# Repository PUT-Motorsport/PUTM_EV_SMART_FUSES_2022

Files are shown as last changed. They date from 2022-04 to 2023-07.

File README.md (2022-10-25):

# PUTM_EV_SMART_FUSES_2022

## Description
The main principle behind the concept of Smart Fuses was adaptability and ease of resetting fuses, what the past designs couldn't achive. The board uses VN9D30Q100F High-side driver with integrated short-circuit detection and programmable interface based on reliable and fast SPI communication. It features 6 programmable channels, two of them are rated for 31,5A maximum flowing current the rest is rated for 14A. As mentioned used uCs can detect when one of the managed boards are

## Quick preview
The Smart Fuses board is responsible for two primary things:
- control over chips with integrated fuses based on mosfets,
- control over assi (auyonomus system status indicator) and buzzer.

## Basic flow chart
Flow chart drawio (1) <br/>
( basic concept of the program's flow, it may or may not change depending on the needs )

## Main Connector Pinout


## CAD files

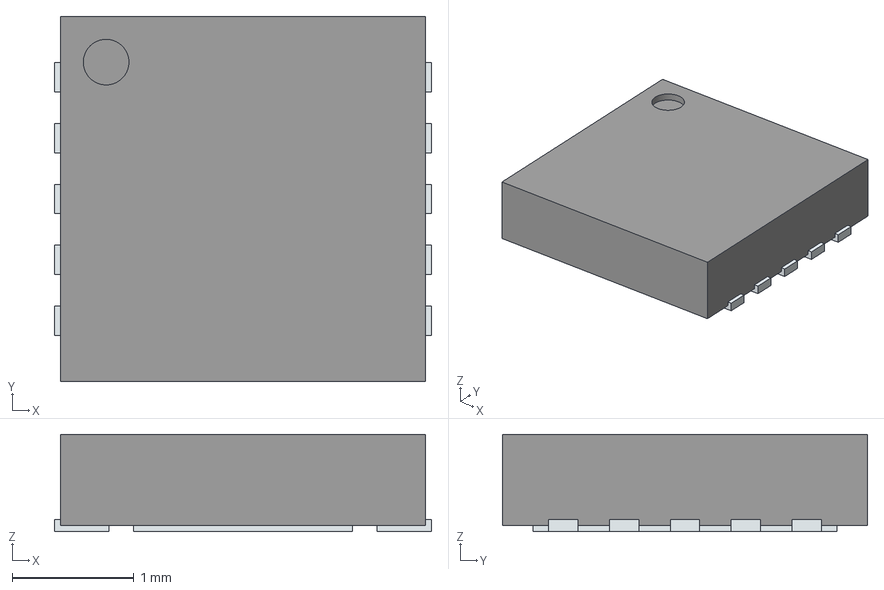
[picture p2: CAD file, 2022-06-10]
hardware/NIS4461MT1TXG/NIS4461MT1TXG.stp
3.10 x 3.00 x 0.8 mm
ThermalPin
PinsArrayLR

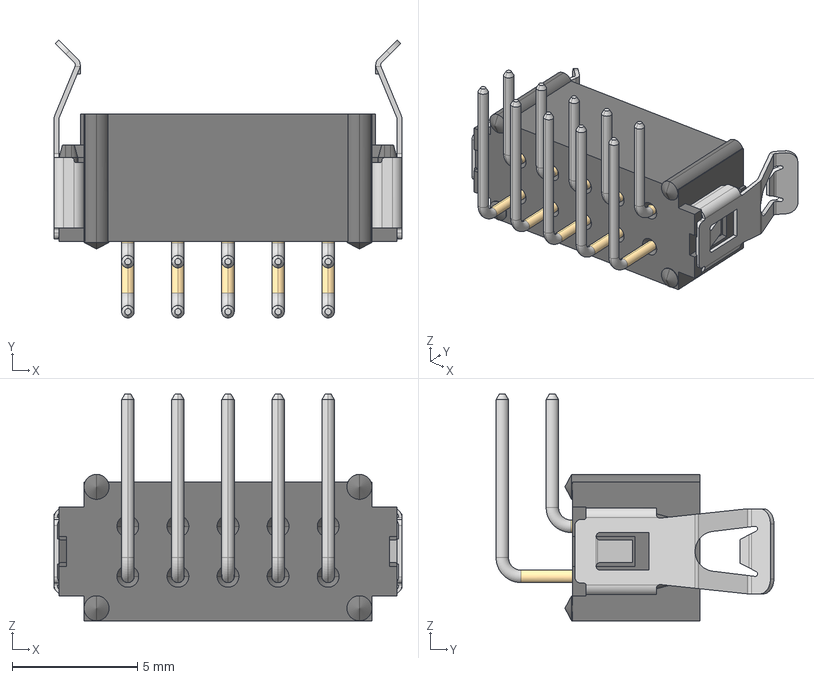
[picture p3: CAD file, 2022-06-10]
hardware/M80-8661022/M80-8661022.stp
13.9 x 11.1 x 9.05 mm
M80-1021098_SEPARATE_ROWS
M80-868-PIN1 x 5
M80-868-PIN2 x 5
M80-001XXXX x 2

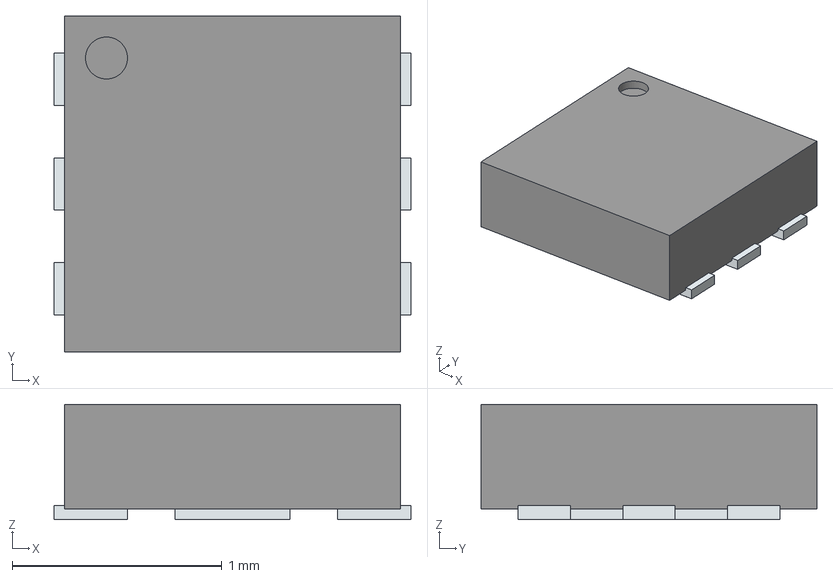
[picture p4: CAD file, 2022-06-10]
hardware/NCS20061MUTAG/NCS20061MUTAG.stp
1.70 x 1.60 x 0.55 mm
ThermalPin
PinsArrayLR

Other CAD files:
hardware/NIS6351MT2TXG/NIS6351MT2TXG.stp
hardware/NCS20061MUTAG/NCS20061MUTAG.stl
hardware/NIS4461MT1TXG/NIS4461MT1TXG.stl
hardware/NIS6351MT2TXG/NIS6351MT2TXG.stl

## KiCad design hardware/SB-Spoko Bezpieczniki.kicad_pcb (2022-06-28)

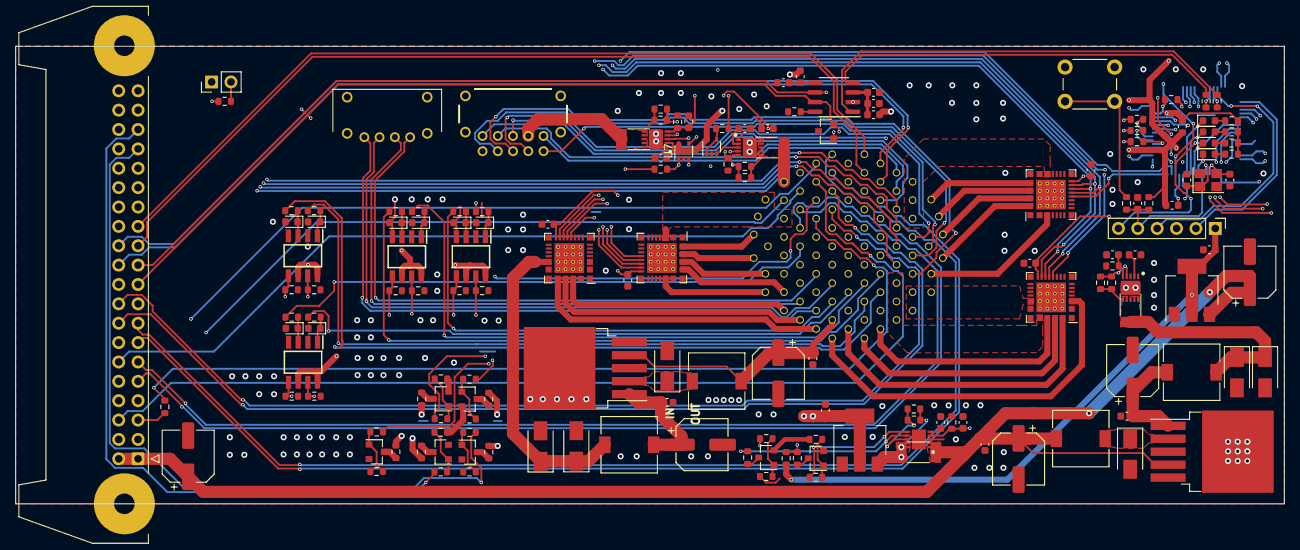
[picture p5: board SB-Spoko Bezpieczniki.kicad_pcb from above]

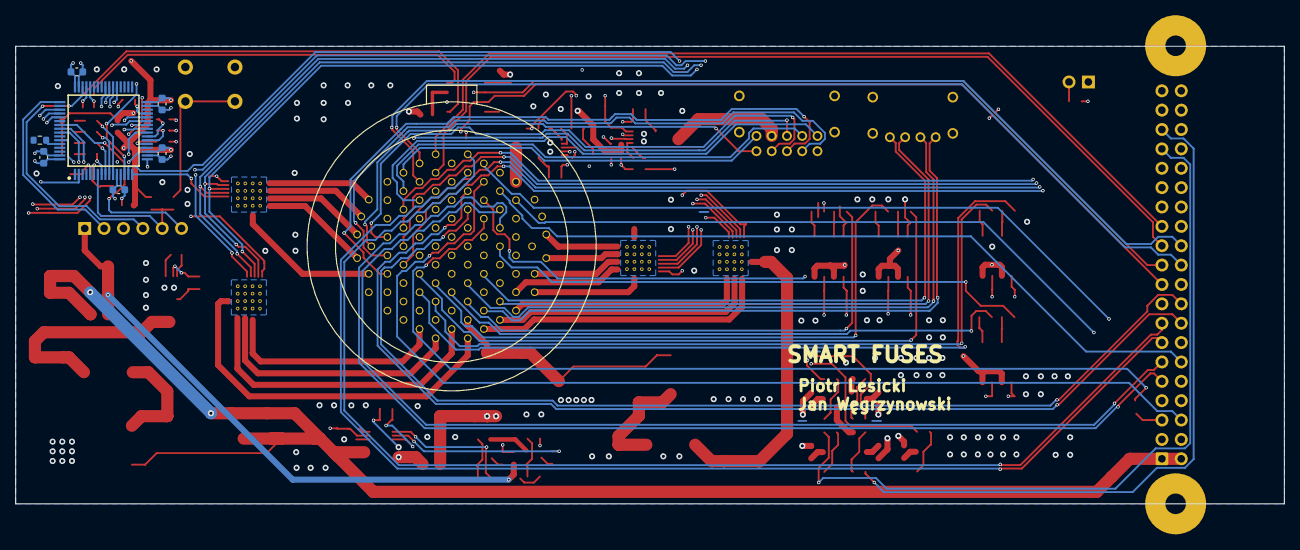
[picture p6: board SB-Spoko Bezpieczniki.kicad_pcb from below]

Board: 4 copper layers, 166.4 x 60.0 mm, 169 parts (8 on the bottom side), 179 nets.

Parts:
C1, C2, C3, C6, C7, C10, C11, C12, C13, C14, C21, C27, C29, C30, C31, C32, C33, C37, C39: 100nF; C_0603_1608Metric
C4, C5, C8, C9, C25, C36: 10pF; CP_Elec_6.3x7.7
C15, C17, C19: 10nF; C_0603_1608Metric
C16, C18, C20: 0; C_0603_1608Metric
C28: 10uF; C_0603_1608Metric
C34, C35: 22pF; C_0603_1608Metric
CLAMP1: 0; C_0603_1608Metric
D1, D2, D11, D12, D13, D14, D15, D16: D_SCH; D_0603_1608Metric
D3, D4: D_ZEN; D_SMA
D5, D6, D7, D8: D_SCH; D_SMA
D18: PESD2CAN.215; SOT-23
D19: I'M FINE; D_0603_1608Metric
D20: I_AM_ON_FIRE!!!; D_0603_1608Metric
D21: COULD_BE_BETTER; D_0603_1608Metric
D22: WHAT_THE_F?; D_0603_1608Metric
F1, F2, F3, F4: Polyfuse; Fuse_2010_5025Metric
FB1, FB2: 60R@100MHz; L_0603_1608Metric
FB3: FB; L_0603_1608Metric
IC1: STM32L4P5RET6; QFP50P1200X1200X160-64N
IC2, IC5, IC6: NIS4461MT1TXG; SON50P300X300X80-11N
IC4: NIS6351MT2TXG; SON50P300X300X80-11N-D
ILIM1, ILIM2, ILIM5, ILIM6, ILIM7, ILIM8: ?; R_0603_1608Metric
ILIM3, ILIM4: 0; R_0603_1608Metric
IMON1, IMON2, IMON3: 1k; R_0603_1608Metric
J1: SWD; PinHeader_1x06_P2.54mm_Vertical
J2: Conn_02x20_Odd_Even; IDC-Header_2x20-1MP_P2.54mm_Latch_Horizontal
J3: M80-8420445
J4: M80-8661022; M808661022
JP1: CAN_EXTARMINATOR; PinHeader_1x02_P2.54mm_Vertical
L1, L3: 22uH; L_7.3x7.3_H3.5
L2, L4: 22uH; L_7.3x7.3_H4.5
L5: L_Small; L_0603_1608Metric
O1, O2, O3, O5: FOD8802DR2_IMG; SOIC127P600X175-8N
Q1, Q2, Q3, Q4, Q5, Q7, Q8: Q_NMOS_GSD; SOT-23
R1, R2, R4, R17, R21, R25, R28, R31, R34, R42, R43, R50, R51, R61: 100; R_0603_1608Metric
R3, R7, R8, R11, R12, R15, R16, R18, R22, R26, R29, R32, R35, R48, R49, R53, R56: 10k; R_0603_1608Metric
R5, R6, R9, R10, R13, R14, R45, R46: --; R_0603_1608Metric
R19: 120; R_0603_1608Metric
R20, R44: 1k; R_0603_1608Metric
R23, R27, R30, R33, R36, R41, R47, R52, R55: 0; R_0603_1608Metric
R24: 100k; R_0603_1608Metric
R37, R38, R39, R40: 470; R_0603_1608Metric
R54: R_Small; R_0603_1608Metric
SW1: RESET; SW_PUSH_6mm
U1: AS222-35PN-933; AS222-35PN-933C-ver4-drill_0.72_size_1.02
U2: LM2596S-12; TO-263-5_TabPin3
U3: LM2596S-5; TO-263-5_TabPin3
U4, U6: LM317_SOT-223; SOT-223-3_TabPin2
U5, U7: MCP6001x-LT; SOT-353_SC-70-5
U11: MCP2558FD-xSN; SOIC-8_3.9x4.9mm_P1.27mm
U12, U13, U14, U15: SMART FUSE; QFN-32_EP_6x6_Pitch0.5mm
Y1: Crystal_GND24_Small; Crystal_SMD_3225-4Pin_3.2x2.5mm

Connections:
3.3V_STM_POWER: C11.1, C12.1, C13.1, C14.1, FB3.2, IC1.19 (VDD_1), IC1.32 (VDD_2), IC1.48 (VDDUSB), IC1.64 (VDD_3), L5.2, R3.1
3.3V_STM_REF+: C10.2, IC1.13 (VDDA/VREF+), L5.1
5V_CONVERT_24V: D4.1 (K), D6.1 (K), F3.1, IC5.6 (SRC_1), IC5.7 (SRC_2), IC5.8 (SRC_3), IC5.9 (SRC_4), IC5.10 (SRC_5), ILIM5.1, ILIM6.1, L4.1
+3V3: C1.2, C30.2, C31.2, C32.2, C37.1, FB2.1, FB3.1, J1.1, O1.6, O1.8, O2.6, O2.8, O3.6, O3.8, O5.6, O5.8, R37.2, R38.2, R39.2, R40.2, R56.2, U4.2 (VO), U5.5 (V+), U7.5 (V+), U12.16 (VDD), U13.16 (VDD), U14.16 (VDD), U15.16 (VDD)
+5V: C7.1, C9.1, C25.1, C36.1, F2.2, FB1.1, IC4.1 (VCC_1), IC4.2 (VCC_2), J2.1, J2.2, L2.2, U3.4 (FB), U4.3 (VI)
+24V: F1.2, F3.2, F4.2, IC2.11 (VCC), IC5.11 (VCC), IC6.11 (VCC), U1.51, U1.52, U1.59, U1.60, U1.61, U1.62, U1.70, U1.71, U1.72, U12.33 (VCC), U13.33 (VCC), U14.33 (VCC), U15.33 (VCC)
/Fusses/BSPD-ESB/EN/FAULT: IC6.3 (EN/FLT), U5.3 (+)
/Fusses/Fuse 3/VOUT_0: U15.3 (OUT_0A), U15.4 (OUT_0B)
/Fusses/Fuse 3/VOUT_1: U15.31 (OUT_1A), U15.32 (OUT_1B)
/Fusses/Supply/IMON: C15.1, IC5.5 (ISENSE), IMON2.1
/Fusses/TSAL/EN/FAULT: IC2.3 (EN/FLT), U7.3 (+)
/Fusses/WATER-POTENTIOMMETER/WATER/POT_EN: IC4.7 (EN), R41.1
/Fusses/WATER-POTENTIOMMETER/WATER/POT_FLAG: IC4.6 (FLAG), R42.1
/Inputs/CAN transreciver/+3V3_VIO: C29.1, FB2.2, U11.5 (VIO)
/Inputs/CAN transreciver/+5V_CAN_VDD: C27.1, C28.1, FB1.2, U11.3 (VDD)
/Inputs/CAN transreciver/SHDN: R47.1, U11.8 (S)
ASMS_24V: U1.55, U14.31 (OUT_1A), U14.32 (OUT_1B)
BAT_HV_24V: U1.15, U15.29 (OUT_2A), U15.30 (OUT_2B)
BOX_24V: U1.3, U12.31 (OUT_1A), U12.32 (OUT_1B)
BOX_DV_24V: U1.83, U1.84, U1.85, U14.25 (OUT_4A), U14.26 (OUT_4B)
BREAK_LIGHT_24V: U1.14, U12.25 (OUT_4A), U12.26 (OUT_4B)
BREAK_LIGHT_GATE: J2.33, R34.1
BREAK_LIGHT_IN: R36.1, U1.32
BSPD/EBS_24V: F4.1, IC6.6 (SRC_1), IC6.7 (SRC_2), IC6.8 (SRC_3), IC6.9 (SRC_4), IC6.10 (SRC_5), ILIM7.1, ILIM8.1, U1.8
BSPD/EBS_IMON: C19.1, IC1.25 (PC5), IC6.5 (ISENSE), IMON3.1
BSPD/EBS_STATE: IC1.24 (PC4), R61.1
BUZZER_CONTROL: R21.1, R52.1
BUZZER_IN: R23.1, U1.12
CAN_RX: R50.1, U11.4 (RXD)
CAN_TX: R51.1, U11.1 (TXD)
CAR_CAN+: D18.2 (A2), J2.19, JP1.1, U1.46, U11.7 (CANH)
CAR_CAN-: D18.1 (A1), J2.21, R19.2, U1.47, U11.6 (CANL)
DASH_24V: U1.98, U13.31 (OUT_1A), U13.32 (OUT_1B)
DIAGPORT_24V: U1.34, U15.25 (OUT_4A), U15.26 (OUT_4B)
DV_SENSE: R45.2, U1.64
DV_SENSE_SIG: IC1.53 (PC12), O5.7, R48.2
ETHERNET_RX+: J3.2, U1.23
ETHERNET_RX-: J3.1, U1.31
ETHERNET_TX+: J3.4, U1.33
ETHERNET_TX-: J3.3, U1.42
FAN_L_24V: U1.95, U13.27 (OUT_3A), U13.28 (OUT_3B)
FAN_MONO_24V: U1.7, U12.21 (OUT_5A), U12.22 (OUT_5B)
FAN_R_24V: U1.94, U13.25 (OUT_4A), U13.26 (OUT_4B)
FIREWALL_SENSE: R46.2, U1.74
FIREWALL_SENSE_SIG: IC1.52 (PC11), O5.5, R49.2
GND: C1.1, C2.2, C3.2, C4.2, C5.2, C6.2, C7.2, C8.2, C9.2, C10.1, C11.2, C12.2, C13.2, C14.2, C15.2, C16.2, C17.2, C18.2, C19.2, C20.2, C21.2, C25.2, C27.2, C28.2, C29.2, C30.1, C31.1, C32.1, C33.2, C34.1, C35.2, C36.2, C37.2, C39.2, CLAMP1.2, D1.2 (A), D2.2 (A), D3.2 (A), D4.2 (A), D5.2 (A), D6.2 (A), D7.2 (A), D8.2 (A), D11.2 (A), D12.2 (A), D13.2 (A), D14.2 (A), D15.2 (A), D16.2 (A), D18.3 (common), IC1.12 (VSSA/VREF-), IC1.18 (VSS_1), IC1.31 (VSS_2), IC1.47 (VSS_3), IC1.63 (VSS_4), IC2.1 (GND), IC4.3 (GND), IC5.1 (GND), IC6.1 (GND), IMON1.2, IMON2.2, IMON3.2, J1.3, J2.3, J2.4, J2.7, J2.14, J2.17, J2.20, J2.31, J2.34, J3.5 (MH1), J3.6 (MH2), J3.7 (MH3), J3.8 (MH4), J4.1, J4.MH1, J4.MH2, J4.MH3, J4.MH4, O1.2, O1.4, O2.2, O2.4, O3.2, O3.4, O5.2, O5.4, Q1.2 (S), Q2.2 (S), Q3.2 (S), Q4.2 (S), Q5.2 (S), Q7.2 (S), Q8.2 (S), R7.1, R8.1, R11.1, R12.1, R15.1, R16.1, R18.2, R22.2, R24.1, R26.2, R29.2, R32.2, R35.2, R44.2, R47.2, R48.1, R49.1, R53.2, SW1.1, U1.16, U1.21, U1.22, U1.29, U1.30, U1.39, U1.40, U1.41, U1.48, U1.49, U1.50, U1.54, U2.3 (GND), U2.5 (~ON/OFF), U3.3 (GND), U3.5 (~ON/OFF), U4.1 (ADJ), U5.2 (V-), U6.1 (ADJ), U7.2 (V-), U11.2 (VSS), U12.17 (GND), U13.17 (GND), U14.17 (GND), U15.17 (GND), Y1.2, Y1.4
HVD_SENSE: R9.2, U1.63
HVD_SENSE_SIG: IC1.40 (PC9), O2.7, R11.2
HV_SENSE: R10.2, U1.73
HV_SENSE_SIG: IC1.39 (PC8), O2.5, R12.2
INVERTER_24V: U1.1, U1.2, U1.10, U12.3 (OUT_0A), U12.4 (OUT_0B)
INVERTER_SENSE: R5.2, U1.53
INVERTER_SENSE_SIG: IC1.51 (PC10), O1.7, R7.2
INV_CAN+: J2.23, U1.57
INV_CAN-: J2.25, U1.56
JETSON_24V: U1.92, U1.93, U1.100, U14.21 (OUT_5A), U14.22 (OUT_5B)
LAPTIMER_24V: U1.96, U13.29 (OUT_2A), U13.30 (OUT_2B)
LED_1_CONTROL: IC1.57 (PB5), R28.1
LED_1_IN: R30.1, U1.4
LED_2_CONTROL: IC1.59 (PB7), R25.1
LED_2_IN: R27.1, U1.11
LIDAR_24V: U1.66, U14.29 (OUT_2A), U14.30 (OUT_2B)
MISO: R2.1, U12.15 (SDO), U13.15 (SDO), U14.15 (SDO), U15.15 (SDO)
MONO_NTC: J2.8, U1.25
MOSI: R4.1, U12.14 (SDI), U13.14 (SDI), U14.14 (SDI), U15.14 (SDI)
MOTEC_24V: U1.6, U12.27 (OUT_3A), U12.28 (OUT_3B)
N_RST: C33.1, IC1.7 (NRST), J1.5, R3.2, R20.2
unnamed: C2.1, C4.1, L3.2, U2.1 (VIN)
unnamed: C3.1, C5.1, L4.2, U3.1 (VIN)
unnamed: C16.1, IC5.2 (DV/DT)
unnamed: C18.1, IC2.2 (DV/DT)
unnamed: C20.1, IC6.2 (DV/DT)
unnamed: CLAMP1.1, IC4.5 (VC_SEL)
unnamed: D1.1 (K), O1.1, R5.1
unnamed: D2.1 (K), O1.3, R6.1
unnamed: D7.1 (K), L1.1, U2.2 (OUT)
unnamed: D8.1 (K), L2.1, U3.2 (OUT)
unnamed: D11.1 (K), O2.1, R9.1
unnamed: D12.1 (K), O2.3, R10.1
unnamed: D13.1 (K), O3.1, R13.1
unnamed: D14.1 (K), O3.3, R14.1
unnamed: D15.1 (K), O5.1, R45.1
unnamed: D16.1 (K), O5.3, R46.1
unnamed: D19.2 (A), R37.1
unnamed: D20.2 (A), R38.1
unnamed: D21.2 (A), R39.1
unnamed: D22.2 (A), R40.1
unnamed: IC1.21 (PA5), R1.2
unnamed: IC1.22 (PA6), R2.2
unnamed: IC1.23 (PA7), R4.2
unnamed: IC1.29 (PB10), R52.2
unnamed: IC1.44 (PA11), R50.2
unnamed: IC1.45 (PA12), R51.2
unnamed: IC1.60 (PH3-BOOT0), R24.2
unnamed: IC2.4 (ILIM), ILIM1.2, ILIM2.2
unnamed: IC4.8 (ILIM), ILIM3.1, ILIM4.1
unnamed: IC5.4 (ILIM), ILIM5.2, ILIM6.2
unnamed: IC6.4 (ILIM), ILIM7.2, ILIM8.2
unnamed: J2.5, R54.1
unnamed: JP1.2, R19.1
unnamed: Q1.1 (G), R21.2, R22.1
unnamed: Q1.3 (D), R23.2
unnamed: Q2.1 (G), R28.2, R29.1
unnamed: Q2.3 (D), R30.2
unnamed: Q3.1 (G), R34.2, R35.1
unnamed: Q3.3 (D), R36.2
unnamed: Q4.1 (G), R31.2, R32.1
unnamed: Q4.3 (D), R33.2
unnamed: Q5.1 (G), R25.2, R26.1
unnamed: Q5.3 (D), R27.2
unnamed: Q7.1 (G), R17.2, R18.1
unnamed: Q7.3 (D), R41.2
unnamed: Q8.1 (G), R42.2, R53.1
unnamed: Q8.3 (D), R55.2
unnamed: R20.1, SW1.2
unnamed: R43.2, U7.1, U7.4 (-)
unnamed: R61.2, U5.1, U5.4 (-)
ODRIVE_24V: U1.86, U1.87, U1.88, U13.21 (OUT_5A), U13.22 (OUT_5B)
POT_?V: C21.1, U1.65, U6.2 (VO)
PUMP_12V: C6.1, C8.1, L1.2, U1.44, U2.4 (FB)
PUMP_24V: D3.1 (K), D5.1 (K), L3.1, U15.21 (OUT_5A), U15.22 (OUT_5B)
RES_COS+: J2.13, U1.36
RES_COS-: J2.15, U1.35
RES_SIN+: J2.9, U1.19
RES_SIN-: J2.11, U1.18
RTDS_GATE: J2.35, R31.1
RTDS_IN: R33.1, U1.13
SCK: R1.1, U12.13 (SCK), U13.13 (SCK), U14.13 (SCK), U15.13 (SCK)
SPARE_1_24V: U1.45, U14.3 (OUT_0A), U14.4 (OUT_0B)
SPARE_1_SENSE: R6.2, U1.20
SPARE_1_SENSE_SIG: IC1.2 (PC13), O1.5, R8.2
SPARE_2_24V: U1.24, U15.27 (OUT_3A), U15.28 (OUT_3B)
SPARE_2_SENSE: R13.2, U1.27
SPARE_2_SENSE_SIG: IC1.37 (PC6), O3.7, R15.2
SPARE_3_SENSE: R14.2, U1.43
SPARE_3_SENSE_SIG: IC1.38 (PC7), O3.5, R16.2
SP_L+: J2.18, U1.38
SP_L-: J2.16, U1.37
SS_0: IC1.15 (PA1), U12.12 (CSN)
SS_1: IC1.16 (PA2), U13.12 (CSN)
SS_2: IC1.17 (PA3), U14.12 (CSN)
SS_3: IC1.20 (PA4), U15.12 (CSN)
STM_???: D22.1 (K), IC1.8 (PC0)
STM_CKL_OUT: C35.1, IC1.6 (PH1-OSC_OUT), Y1.1
STM_CLK_IN: C34.2, IC1.5 (PH0-OSC_IN), Y1.3
STM_FATAL_ERROR: D20.1 (K), IC1.9 (PC1)
STM_OK: D19.1 (K), IC1.11 (PC3)
STM_SOFT_ERROR: D21.1 (K), IC1.10 (PC2)
SWCLK: IC1.49 (PA14), J1.2
SWDIO: IC1.46 (PA13), J1.4
SWO: IC1.55 (PB3), J1.6
TSAL_24V: F1.1, IC2.6 (SRC_1), IC2.7 (SRC_2), IC2.8 (SRC_3), IC2.9 (SRC_4), IC2.10 (SRC_5), ILIM1.1, ILIM2.1, J4.9
TSAL_DASH_LED_GREEN: J4.3, U1.91
TSAL_DASH_LED_RED: J4.2, U1.90
TSAL_HV_AIR1: J4.6, U1.69
TSAL_HV_AIR2: J4.10, U1.77
TSAL_HV_BAT_SIG: J4.7, U1.78
TSAL_HV_INV_SIG: J4.8, U1.58
TSAL_IMON: C17.1, IC1.14 (PA0), IC2.5 (ISENSE), IMON1.1
TSAL_LED_GREEN: J4.5, U1.97
TSAL_LED_RED: J4.4, U1.89
TSAL_STATE: IC1.27 (PB1), R43.1
TSAL/ASSI_24V: U1.5, U12.29 (OUT_2A), U12.30 (OUT_2B)
USB_DEBUG_DM: J2.24, U1.68
USB_DEBUG_DP: J2.22, U1.67
WATER_1_PRESSURE: J2.6, U1.26
WATER_2_PRESSURE: R54.2, U1.28
WATER_5V: F2.1, IC4.9 (SRC_1), IC4.10 (SRC_2), ILIM3.2, ILIM4.2, U1.75, U6.3 (VI)
WATER_NTC_1: J2.12, U1.17
WATER_NTC_2: J2.10, U1.9
WATER/POT_ENABLE: IC1.28 (PB2), R17.1
WATER/POT_IMON: C39.1, IC1.26 (PB0), IC4.4 (IMON), R44.1
WATER/POT_STATE: IC1.56 (PB4), R55.1, R56.1
WHEEL_SPEED_1_24V: U1.99, U13.3 (OUT_0A), U13.4 (OUT_0B)
WHEEL_SPEED_2_24V: U1.76, U14.27 (OUT_3A), U14.28 (OUT_3B)
WSS_FL: J2.38, U1.80
WSS_FR: J2.40, U1.82
WSS_RL: J2.37, U1.79
WSS_RR: J2.39, U1.81

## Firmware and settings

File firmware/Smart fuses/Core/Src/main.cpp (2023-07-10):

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
/* Includes ------------------------------------------------------------------*/
#include "main.h"
#include "adc.h"
#include "can.h"
#include "spi.h"
#include "gpio.h"

/* USER CODE BEGIN Includes */
#include "stm32l4xx_hal_spi.h"
#include "timer.h"
#include "fuse.hpp"
#include "gpio elements.hpp"
#include "PUTM_EV_CAN_LIBRARY/lib/can_interface.hpp"
#include "math.h"
#include "algorithm"
#include "etl/queue.h"
#include "tokens.hpp"
#include "gpio handler.hpp"
#include "buzzer.hpp"

/* USER CODE END Includes */


/* USER CODE BEGIN PV */

class Device
{
	public:
		static void raise(PUTM_CAN::SF_states);
		static void clear(PUTM_CAN::SF_states);
		static void handleState();

	private:
		inline static PUTM_CAN::SF_states state = PUTM_CAN::SF_states::Ok;
};

/* USER CODE END PV */

void SystemClock_Config(void);
/* USER CODE BEGIN PFP */

void initCAN();

HAL_StatusTypeDef sendCanFramePassiveElements();
HAL_StatusTypeDef sendCanFrameLegendaryDVAndSupply();
HAL_StatusTypeDef sendCanFrameSupply();
HAL_StatusTypeDef sendCanFrameSafety();


/* USER CODE END PFP */

/* USER CODE BEGIN 0 */

const bool use_tc_main_ts_on_for_fan_control = true;

const size_t safety_sapre_2 = 0;
const size_t safety_sapre_3 = 1;
const size_t safety_hv = 2;
const size_t safety_hvd = 3;
const size_t safety_inverter = 4;
const size_t safety_firewall = 5;
const size_t safety_dv = 6;
const size_t safety_sapre_1 = 7;

const uint32_t buzzer_signal_lenght = 9000;

bool water_pot_kek;

GpioOutElement led_error(GPIOC, GPIO_PIN_0, true);//(GPIOB, GPIO_PIN_10, false);
GpioOutElement led_warning_2(GPIOC, GPIO_PIN_1, true);
GpioOutElement led_warning_1(GPIOC, GPIO_PIN_2, true);
GpioOutElement led_ok(GPIOC, GPIO_PIN_3, true);

GpioOutElement led_1_control(GPIOB, GPIO_PIN_5, false);
GpioOutElement led_2_control(GPIOB, GPIO_PIN_7, false);

Buzzer buzzer_control(GPIOB, GPIO_PIN_10, false, buzzer_signal_lenght);//(GPIOC, GPIO_PIN_0, false, buzzer_signal_lenght);

GpioOutElement water_pot_enable(GPIOB, GPIO_PIN_2, true);

GpioInElement water_pot_state(GPIOB, GPIO_PIN_4, false);

GpioInElement spare_2_sense_sig(GPIOC, GPIO_PIN_6, false);
GpioInElement spare_3_sense_sig(GPIOC, GPIO_PIN_7, false);
GpioInElement hv_sense_sig(GPIOC, GPIO_PIN_8, false);
GpioInElement hvd_sense_sig(GPIOC, GPIO_PIN_9, false);
GpioInElement inverter_sense_sig(GPIOC, GPIO_PIN_10, false);
GpioInElement firewall_sense_sig(GPIOC, GPIO_PIN_11, false);
GpioInElement dv_sense_sig(GPIOC, GPIO_PIN_12, false);
GpioInElement spare_1_sense_sig(GPIOC, GPIO_PIN_13, false);

CAN_FilterTypeDef can_filtering_config;

//debug stuff
std::array < SmartFuseState, number_of_fuses > fuses_states;
std::array < std::array < ChannelState, number_of_channels_per_fuse >, number_of_fuses > channels_states;
std::array < std::array < float, number_of_channels_per_fuse >, number_of_fuses > channels_currents;
std::array < bool, 8 > safeties { };
std::array < HAL_StatusTypeDef, 6 > frame_send_fail { };

PUTM_CAN::SF_states device_state;

SmartFuseHandler < number_of_fuses > sf_handler;

GpioOutHandler assi_leds_handler;

auto prev_ass_status = PUTM_CAN::AutonomousSystemStatus::Off;

/* USER CODE END 0 */

/**
  * @brief  The application entry point.
  * @retval int
  */
int main(void)
{
  /* USER CODE BEGIN 1 */

	ChannelSettings std_channel_setting
	{
		.active = true,
		.latch_off_time_out = 0x2,
		.sampling_mode = SamplingMode::Filtered,
		.duty_cycle = 0x3ff,
		.clamping_currents = { 0.f, 10.f }
	};

	std::array < ChannelSettings, number_of_channels_per_fuse > std_fuse_channels_settings
	{
		std_channel_setting,
		std_channel_setting,
		std_channel_setting,
		std_channel_setting,
		std_channel_setting,
		std_channel_setting
	};

	//----------------------------------------------------------------------------------------
	/*
	 * fuse 0
	 * channel 0: inverter
	 * channel 1: front box
	 * channel 2: tsal/assi
	 * channel 3: motec
	 * channel 4: break light
	 * channel 5: fan mono
	 */
	sf_handler.emplaceBack(GPIOA, GPIO_PIN_1, &hspi1, std_fuse_channels_settings);

	//----------------------------------------------------------------------------------------
	/*
	 * fuse 1
	 * channel 0: wheel speed
	 * channel 1: dash
	 * channel 2: laptimer
	 * channel 3: fan l
	 * channel 4: fan r
	 * channel 5: odrive
	 * action: fan control
	 */
	std::array < ChannelSettings, number_of_channels_per_fuse > fuse_1_channels_settings
	{
		std_channel_setting,
		std_channel_setting,
		std_channel_setting,
		{
			// fan l
			.active = true,
			.latch_off_time_out = 0x2,
			.sampling_mode = SamplingMode::Filtered,
			.duty_cycle = 0x000,
			.clamping_currents = { 0.f, 10.f }
		},
		{
			// fan r
			.active = true,
			.latch_off_time_out = 0x2,
			.sampling_mode = SamplingMode::Filtered,
			.duty_cycle = 0x000,
			.clamping_currents = { 0.f, 10.f }
		},
		std_channel_setting
	};
	sf_handler.emplaceBack(GPIOA, GPIO_PIN_2, &hspi1, fuse_1_channels_settings, 100, [](SmartFuse* sf)
	{

		static uint16_t previous_setting = 0;

		uint16_t setting = 0;

		if constexpr(!use_tc_main_ts_on_for_fan_control)
		{
			/*
			 * min difference for for the change in fan speed to occur
			 */
			constexpr uint16_t min_diff = 10;
			/*
			 * interpolation results for: (20, 0), (30, 200), (40, 500), (50, 800), (60, 1023)
			 */
			constexpr float a = 0.0328571429f;
			constexpr float b = 23.8314285714f;
			constexpr float c = - 507.8f;


			auto tc_inv_temp = static_cast<float>(PUTM_CAN::can.get_tc_temperatures().inverter);
			auto result = a * tc_inv_temp * tc_inv_temp + b * tc_inv_temp + c;
			setting = static_cast<uint16_t>(etl::clamp(result, 0.f, 1023.f));

			if(std::abs(previous_setting - setting) >= min_diff)
			{
				// fan left
				sf->setChannelDutyCykle(Channel::c3, setting);
				// fan right
				sf->setChannelDutyCykle(Channel::c4, setting);

				previous_setting = setting;
			}
		}
		else
		{
			auto tc_on = PUTM_CAN::can.get_tc_main().tractive_system_on;

			if(tc_on) setting = 1023;
			else setting = 0;

			if(setting != previous_setting)
			{
				// fan left
				sf->setChannelDutyCykle(Channel::c3, setting);
				// fan right
				sf->setChannelDutyCykle(Channel::c4, setting);

				previous_setting = setting;
			}
		}
	});

	//----------------------------------------------------------------------------------------
	/*
	 * fuse 2
	 * channel 0: spare 1
	 * channel 1: asms/safety
	 * channel 2: lidar
	 * channel 3: wheel speed
	 * channel 4: box dv
	 * channel 5: jetson
	 */
	sf_handler.emplaceBack(GPIOA, GPIO_PIN_3, &hspi1, std_fuse_channels_settings);

	//----------------------------------------------------------------------------------------
	/*
	 * fuse 3
	 * channel 0: --
	 * channel 1: --
	 * channel 2: bat hv
	 * channel 3: spare 2
	 * channel 4: diagport
	 * channel 5: pump
	 */
	sf_handler.emplaceBack(GPIOA, GPIO_PIN_4, &hspi1, std_fuse_channels_settings);

	//----------------------------------------------------------------------------------------

	assi_leds_handler.add(&led_1_control, 500, 500, led_1_control.token_source.getToken());
	assi_leds_handler.add(&led_2_control, 500, 500, led_2_control.token_source.getToken());
	assi_leds_handler.add(&buzzer_control, 100, 100, buzzer_control.token_source.getToken());

  /* USER CODE END 1 */

  /* MCU Configuration--------------------------------------------------------*/

  /* Reset of all peripherals, Initializes the Flash interface and the Systick. */
  HAL_Init();

  /* Configure the system clock */
  SystemClock_Config();

  /* Initialize all configured peripherals */
  MX_GPIO_Init();
  MX_CAN1_Init();
  MX_SPI1_Init();
  MX_ADC1_Init();
  /* USER CODE BEGIN 2 */

	sf_handler.initAll();
	initCAN();
	water_pot_enable.activate();
	led_2_control.deactivate();
	led_1_control.deactivate();

	led_ok.deactivate();
	led_warning_1.deactivate();
	led_warning_2.deactivate();
	led_error.deactivate();

  /* USER CODE END 2 */

  /* Infinite loop */
  /* USER CODE BEGIN WHILE */

	sf_handler.enableAll();

	led_ok.activate();

	Timer timer_can_send_main_frame(10);
	Timer timer_can_send_other_frames(25);

	std::array < GpioInElement, 8 > optos
	{
		spare_2_sense_sig,
		spare_3_sense_sig,
		hv_sense_sig,
		hvd_sense_sig,
		inverter_sense_sig,
		firewall_sense_sig,
		dv_sense_sig,
		spare_1_sense_sig
	};

	while (true)
	{
		//----------------------------------------------------------------------------------------
		// handle smart fuses and show as Ok/Warnings/Error
		Device::handleState();
		auto state = sf_handler.handleAll();
		if(state != SmartFuseState::Ok) Device::raise(PUTM_CAN::SF_states::Warning_1);
		else Device::clear(PUTM_CAN::SF_states::Warning_1);

		// debug stuff
		fuses_states = sf_handler.getStates();
		channels_states = sf_handler.getChannelsStates();
		channels_currents = sf_handler.getChannelsCurrents();

		//----------------------------------------------------------------------------------------
		// handle safety
		for (size_t i = 0; i < optos.size(); i++)
			safeties[i] = optos[i].isActive();

		//----------------------------------------------------------------------------------------
		// transmit receive can and handle
		// main frame
		if(timer_can_send_main_frame.checkIfTimedOutAndReset())
		{
			PUTM_CAN::SF_main sf_main
			{
				.device_state =	device_state,
				.fuse_0_state = static_cast<PUTM_CAN::SmartFuseState>(fuses_states[0]),
				.fuse_1_state = static_cast<PUTM_CAN::SmartFuseState>(fuses_states[1]),
				.fuse_2_state = static_cast<PUTM_CAN::SmartFuseState>(fuses_states[2]),
				.fuse_3_state = static_cast<PUTM_CAN::SmartFuseState>(fuses_states[3])
			};

			PUTM_CAN::Can_tx_message<PUTM_CAN::SF_main> can_sender(sf_main, PUTM_CAN::can_tx_header_SF_MAIN);

			if(can_sender.send(hcan1) != HAL_StatusTypeDef::HAL_OK)
				Device::raise(PUTM_CAN::SF_states::Error);
			else Device::clear(PUTM_CAN::SF_states::Error);
		}

		// other frames
		if(timer_can_send_other_frames.checkIfTimedOutAndReset())
		{
			auto can_state = HAL_OK;
			static size_t send_frame = 0;

			switch (send_frame)
			{
				case 0: can_state = sendCanFramePassiveElements(); break;
				case 1: can_state = sendCanFrameLegendaryDVAndSupply(); break;
				case 2: can_state = sendCanFrameSupply(); break;
				case 3: can_state = sendCanFrameSafety(); break;
			}

			frame_send_fail[send_frame] = can_state;

			if(can_state != HAL_OK)
				Device::raise(PUTM_CAN::SF_states::Warning_2);
			else Device::clear(PUTM_CAN::SF_states::Warning_2);

			send_frame++;
			if(send_frame > 5) send_frame = 0;
		}

		//----------------------------------------------------------------------------------------
		// Handle ASSI

		assi_leds_handler.handle();
		buzzer_control.handle();

		auto ass_status = PUTM_CAN::can.get_dv_ass().status;//PUTM_CAN::AutonomousSystemStatus::Emergency;//

		if(prev_ass_status != ass_status)
		{
			prev_ass_status = ass_status;
			switch (ass_status)
			{
				//all OFF
				case PUTM_CAN::AutonomousSystemStatus::Off:
					led_1_control.deactivate();
					led_1_control.token_source.stop();
					led_2_control.deactivate();
					led_2_control.token_source.stop();

					buzzer_control.token_source.stop();
					break;

				// orange / yellow ON
				case PUTM_CAN::AutonomousSystemStatus::Ready:
					led_1_control.activate();
					led_1_control.token_source.stop();
					led_2_control.deactivate();
					led_2_control.token_source.stop();

					buzzer_control.token_source.stop();
					break;

				// orange / yellow PULSING
				case PUTM_CAN::AutonomousSystemStatus::Driving:
					led_1_control.deactivate();
					led_1_control.token_source.start();
					led_2_control.deactivate();
					led_2_control.token_source.stop();

					buzzer_control.token_source.stop();
					break;

				// blue PULSING, buzzer PULSING
				case PUTM_CAN::AutonomousSystemStatus::Emergency:
					led_1_control.deactivate();
					led_1_control.token_source.stop();
					led_2_control.deactivate();
					led_2_control.token_source.start();

					buzzer_control.token_source.start();
					break;

				// blue ON
				case PUTM_CAN::AutonomousSystemStatus::Finished:
					led_1_control.deactivate();
					led_1_control.token_source.stop();
					led_2_control.activate();
					led_2_control.token_source.stop();

					buzzer_control.token_source.stop();
					break;
			}
		}

    /* USER CODE END WHILE */

    /* USER CODE BEGIN 3 */
	}

  /* USER CODE END 3 */
}

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
/* USER CODE BEGIN 4 */

void Device::handleState()
{
	led_ok.deactivate();
	led_warning_1.deactivate();
	led_warning_2.deactivate();
	led_error.deactivate();

	switch (Device::state)
	{
		case PUTM_CAN::SF_states::Ok:
			led_ok.activate(); break;
		case PUTM_CAN::SF_states::Warning_1:
			led_warning_1.activate(); break;
		case PUTM_CAN::SF_states::Warning_2:
			led_warning_2.activate(); break;
		case PUTM_CAN::SF_states::Error:
			led_error.activate();
	}
}

void Device::raise(PUTM_CAN::SF_states state)
{
	if (int(state) <= int(Device::state)) return;
	Device::state = state;
}

void Device::clear(PUTM_CAN::SF_states state)
{
	if (state != Device::state) return;
	Device::state = PUTM_CAN::SF_states::Ok;
}

void initCAN()
{
	can_filtering_config.FilterBank = 0;
	can_filtering_config.FilterMode = CAN_FILTERMODE_IDMASK;
	can_filtering_config.FilterScale = CAN_FILTERSCALE_32BIT;
	can_filtering_config.FilterIdHigh = 0x0000;
	can_filtering_config.FilterIdLow = 0x0000;
	can_filtering_config.FilterMaskIdHigh = 0x0000;
	can_filtering_config.FilterMaskIdLow = 0x0000;
	can_filtering_config.FilterFIFOAssignment = CAN_RX_FIFO0;
	can_filtering_config.FilterActivation = ENABLE;
	can_filtering_config.SlaveStartFilterBank = 14;

	if ( HAL_CAN_ConfigFilter(&hcan1, &can_filtering_config) != HAL_OK )
		Error_Handler();

	if ( HAL_CAN_Start(&hcan1) != HAL_OK )
		Error_Handler();

	if ( HAL_CAN_ActivateNotification(&hcan1, CAN_IT_RX_FIFO0_MSG_PENDING) != HAL_OK )
		Error_Handler();
}

HAL_StatusTypeDef sendCanFramePassiveElements()
{
	auto& sf_buff = sf_handler.smart_fuses;
	auto wat_pot_state = (water_pot_state.isActive() ? PUTM_CAN::ChannelState::Ok : PUTM_CAN::ChannelState::Error);

		PUTM_CAN::SF_PassiveElements frame
		{
			.break_light = static_cast<PUTM_CAN::ChannelState>(sf_buff[0].getChannelState(fuse_0_break_light)),
			.fan_mono = static_cast<PUTM_CAN::ChannelState>(sf_buff[0].getChannelState(fuse_0_fan_mono)),
			.fan_l = static_cast<PUTM_CAN::ChannelState>(sf_buff[1].getChannelState(fuse_1_fan_l)),
			.fan_r = static_cast<PUTM_CAN::ChannelState>(sf_buff[1].getChannelState(fuse_1_fan_r)),
			.wheel_speed_1 = static_cast<PUTM_CAN::ChannelState>(sf_buff[1].getChannelState(fuse_1_wheel_speed_1)), // idk which is left and which is right
			.wheel_speed_2 = static_cast<PUTM_CAN::ChannelState>(sf_buff[2].getChannelState(fuse_2_wheel_speed_2)), // idk which is left and which is right or front or whatever
			.water_potentiometer = wat_pot_state, // they are together
			.tsal_assi = static_cast<PUTM_CAN::ChannelState>(sf_buff[0].getChannelState(fuse_0_tsal_assi)) // supply for leds ex.
		};

		PUTM_CAN::Can_tx_message<PUTM_CAN::SF_PassiveElements> sender(frame, PUTM_CAN::can_tx_header_SF_PASSIVEELEMENTS);

		return sender.send(hcan1);
}

HAL_StatusTypeDef sendCanFrameLegendaryDVAndSupply()
{
	auto& sf_buff = sf_handler.smart_fuses;

		PUTM_CAN::SF_LegendaryDVAndSupply frame
		{
			.lidar = static_cast<PUTM_CAN::ChannelState>(sf_buff[2].getChannelState(fuse_2_lidar)),
			.box_dv = static_cast<PUTM_CAN::ChannelState>(sf_buff[2].getChannelState(fuse_2_box_dv)),
			.jetson = static_cast<PUTM_CAN::ChannelState>(sf_buff[2].getChannelState(fuse_2_jetson)),
			.odrive = static_cast<PUTM_CAN::ChannelState>(sf_buff[1].getChannelState(fuse_1_odrive)),
			.tsal = static_cast<PUTM_CAN::ChannelState>(ChannelState::Ok),
			.bspd_esb = static_cast<PUTM_CAN::ChannelState>(ChannelState::Ok),
			.spare_1 = static_cast<PUTM_CAN::ChannelState>(sf_buff[2].getChannelState(fuse_2_spare_1)),
			.spare_2 = static_cast<PUTM_CAN::ChannelState>(sf_buff[3].getChannelState(fuse_3_spare_2))
		};

		PUTM_CAN::Can_tx_message<PUTM_CAN::SF_LegendaryDVAndSupply> sender(frame, PUTM_CAN::can_tx_header_SF_LEGENDARYDVANDSUPPLY);

		return sender.send(hcan1);
}

HAL_StatusTypeDef sendCanFrameSupply()
{
	auto& sf_buff = sf_handler.smart_fuses;

		PUTM_CAN::SF_Supply frame
		{
			.inverter = static_cast<PUTM_CAN::ChannelState>(sf_buff[0].getChannelState(fuse_0_inverter)),
			.front_box = static_cast<PUTM_CAN::ChannelState>(sf_buff[0].getChannelState(fuse_0_front_box)),
			.dash = static_cast<PUTM_CAN::ChannelState>(sf_buff[1].getChannelState(fuse_1_dash)),
			.laptimer = static_cast<PUTM_CAN::ChannelState>(sf_buff[1].getChannelState(fuse_1_lapimer)),
			.bat_hv = static_cast<PUTM_CAN::ChannelState>(sf_buff[3].getChannelState(fuse_3_bat_hv)),
			.diagport = static_cast<PUTM_CAN::ChannelState>(sf_buff[3].getChannelState(fuse_3_diagport)),
			.pomp = static_cast<PUTM_CAN::ChannelState>(sf_buff[3].getChannelState(fuse_3_pump)),
			.motec = static_cast<PUTM_CAN::ChannelState>(sf_buff[0].getChannelState(fuse_0_motec))
		};

		PUTM_CAN::Can_tx_message<PUTM_CAN::SF_Supply> sender(frame, PUTM_CAN::can_tx_header_SF_SUPPLY);

		return sender.send(hcan1);
}

HAL_StatusTypeDef sendCanFrameSafety()
{
		PUTM_CAN::SF_safety frame
		{
			.firewall = safeties[safety_firewall],
			.hvd = safeties[safety_hvd],
			.inverter = safeties[safety_inverter],
			.dv = safeties[safety_dv],
			/*
			 * TODO: tsms not present should be hv_sense i guess
			 */
			.tsms = safeties[safety_inverter]
		};

		PUTM_CAN::Can_tx_message<PUTM_CAN::SF_safety> sender(frame, PUTM_CAN::can_tx_header_SF_SAFETY);

		return sender.send(hcan1);
}


/* USER CODE END 4 */
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


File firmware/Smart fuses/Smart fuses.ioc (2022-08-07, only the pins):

Mcu.UserName=STM32L4P5RGTx
PA0.Signal=ADCx_IN5
PA1.Signal=GPIO_Output
PA11.Signal=CAN1_RX
PA12.Signal=CAN1_TX
PA2.Signal=GPIO_Output
PA3.Signal=GPIO_Output
PA4.Signal=GPIO_Output
PA5.Signal=SPI1_SCK
PA6.Signal=SPI1_MISO
PA7.Signal=SPI1_MOSI
PB0.Signal=ADCx_IN15
PB1.Signal=ADCx_IN16
PB10.Signal=GPIO_Output
PB2.Signal=GPIO_Output
PB5.Signal=GPIO_Output
PB7.Signal=GPIO_Output
PB9.Signal=GPIO_Output
PC0.Signal=GPIO_Output
PC1.Signal=GPIO_Output
PC10.Signal=GPIO_Input
PC11.Signal=GPIO_Input
PC12.Signal=GPIO_Input
PC13.Signal=GPIO_Input
PC2.Signal=GPIO_Output
PC3.Signal=GPIO_Output
PC4.Signal=ADCx_IN13
PC5.Signal=ADCx_IN14
PC6.Signal=GPIO_Input
PC7.Signal=GPIO_Input
PC8.Signal=GPIO_Input
PC9.Signal=GPIO_Input

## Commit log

2021-12-14 Smart fusses first commit
    [CAN transreciver.sch, Digital_Output.sch, N_MOSFET.sch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]
2021-12-14 changed the name of the folder from SB... -> hardware
    [CAN transreciver.sch, Digital_Output.sch, N_MOSFET.sch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]
2021-12-14 removed power_2, becaouse unnecessary
2021-12-17 1. added 2X20 connector, \n 2. changed the footprints of schootkies and zenner diodes to a bigger ones, \n 3. changed pcb layout entirely couse duck me, that connector i too duking BIG.
    [Digital_Output.sch, N_MOSFET.sch, Optocoupler.sch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]
2022-01-09 Updated to be compatible with KiCad 6.0.0, changed chematics layouts to fit in A4 worksheet and finished routing the rest of the signals.
    [CAN transreciver.kicad_sch, CAN transreciver.sch, Connectors.kicad_sch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]
2022-01-16 changed clock and 5v converter coils, footprints rearrange commponets to fit the need now the board connector is vertical not horizontal relative to the pcb's longest side
    [CAN transreciver.kicad_sch, Digital_Output.kicad_sch, Fusses.kicad_sch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]
2022-01-22 minor improvements
    [Connectors.kicad_sch, Digital_Output.kicad_sch, Fusses.kicad_sch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]
2022-01-23 Plz Janek powiedz mi ze jest ok
    [SB-Spoko Bezpieczniki.kicad_pcb]
2022-01-23 added traceswo from pin 55 to progrmator
    [Digital_Output.kicad_sch, Inputs.kicad_sch, N_MOSFET.kicad_sch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]
2022-01-23 preproduction bug fixes
    [Digital_Output.kicad_sch, SB-Spoko Bezpieczniki.kicad_pcb, SB-Spoko Bezpieczniki.kicad_sch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]
2022-04-20 lets gooooooooooooooooooooooooooooooooooooo fuses workgit add *git add *git add *git add *git add *git add *
2022-04-20 fuses.h strucure development
2022-05-10 new gpio element lib for easier gpio management, updated fuses lib
2022-05-12 neet the lib for smart fuses works
2022-05-28 changed the order of pins, and started first changes for a v2 board
2022-05-28 currected autosport connector
2022-05-29 currected sf autosport connector, also updated firmware to better handle the showing of board status throught the on board LEDs
    [Connectors.kicad_sch, Digital_Output.kicad_sch, Fusses.kicad_sch]
2022-06-07 major schematic update, changed optocouplers for different, added new fuses for 5v supply for water and potentiometers and 24v supply for BSPD/ESB, updated autosport connector, and some other changes
    [Connectors.kicad_sch, Fusses.kicad_sch, Inputs.kicad_sch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]
2022-06-10 changed some footprints for clarity, and made some progress on board
    [Connectors.kicad_sch, Fusses.kicad_sch, Inputs.kicad_sch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]
2022-06-12 finished new wersion of the board
    [CAN transreciver.kicad_sch, Connectors.kicad_sch, Fusses.kicad_sch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]
2022-06-13 debuged the board, changed one opto for mosfet, changed the way water and potentiometers were supplied. Also standrised opamps (yoinked opamps from data Data_Acquisition_Cards)
    [CAN transreciver.kicad_sch, Connectors.kicad_sch, Fusses.kicad_sch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]
2022-06-16 currected TSAL, cause it can't be controled via external logic
    [Fusses.kicad_sch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]
2022-06-20 curected tsal supply, added sending of all smartfuses related frames, changed a nameing scheme for some classes/structs ex. for better clarity
2022-06-21 nameing scheme update
    [Connectors.kicad_sch, Fusses.kicad_sch, N_MOSFET.kicad_sch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]
2022-06-21 extended smart fuse lib, added a fan control
2022-06-28 saved current progress
    [SB-Spoko Bezpieczniki.kicad_pcb]
2022-07-22 changed the software to work on a new board
2022-09-28 Added ASSI control, added GpioOutHandler responsible for overseeing the timing for blinking leds, added a type of GpioOutElement - Buzzer responsible for custom buzzer control
    [gpio handler.cpp, main.cpp]
2023-07-10 increased max current and changed reading mode of sf to filtered

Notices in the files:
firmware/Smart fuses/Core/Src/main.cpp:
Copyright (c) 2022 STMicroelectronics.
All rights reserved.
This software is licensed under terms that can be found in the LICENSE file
